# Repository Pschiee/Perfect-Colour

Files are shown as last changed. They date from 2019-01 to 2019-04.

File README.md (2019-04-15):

<p align="center">
	<a href="https://enquiriesperfectco.wixsite.com/perfectcolour">
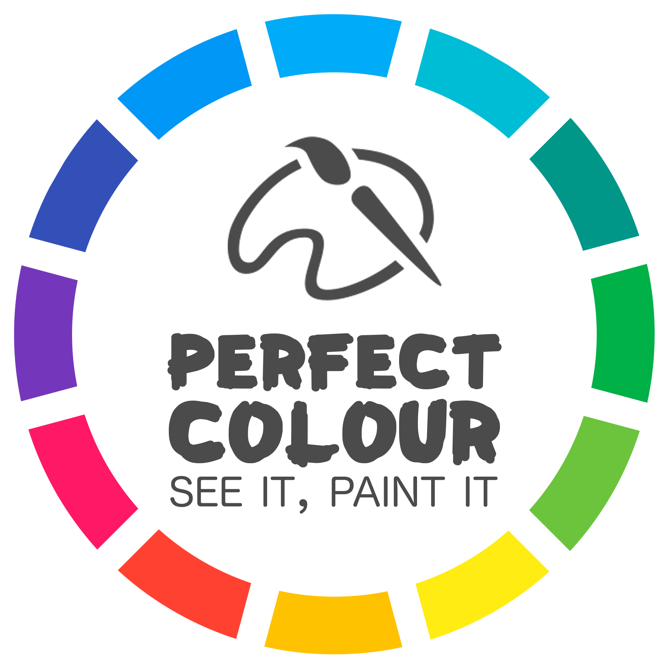
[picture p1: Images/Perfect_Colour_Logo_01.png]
Perfect Colour
	</a></p>

<!-- display the social media buttons in your README -->

[][1]
[][2]

<!-- links to social media icons -->
<!-- no need to change these -->

<!-- icons with padding -->

[1.1]: http://i.imgur.com/tXSoThF.png (twitter icon with padding)
[2.1]: http://i.imgur.com/P3YfQoD.png (facebook icon with padding)

<!-- links to your social media accounts -->
<!-- update these accordingly -->

[1]: https://twitter.com/PerfectColour1
[2]: https://www.facebook.com/Perfect-Colour-2317584661807012/

# Perfect Colour 

Welcome to the Github for Perfect Colour - The paint system to automatically dispense the colour of paint that you want.

<p align="center">
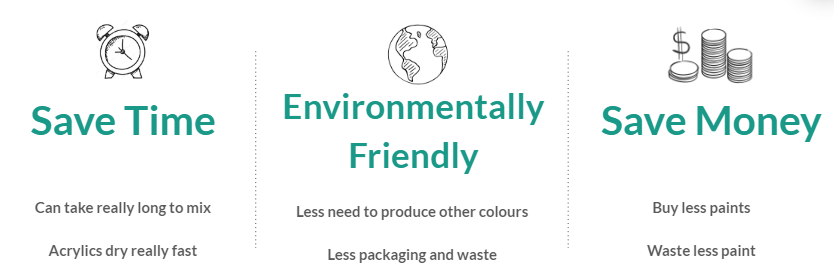
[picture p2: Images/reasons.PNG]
	</a></p>

Through the use of the GUI, you can select the colour using two different methods: by using the colour wheel or by selecting the colour you wish on an image which can then be made for you. 

# Table of Contents
1. [Installation](#installation)
2. [How to get started](#how-to-get-started)
3. [Using the application](#using-the-application)
4. [Demonstrartion](#demonstration)
5. [FAQs](#faqs)
6. [Further Information](#further-information)
7. [Credits](#credits)

## Installation

On the terminal of a Raspberry Pi type the following:

`git clone https://github.com/Pschiee/Perfect-Colour.git`

`cd Software`

`qmake`

`make`

`./AppPerfectColour`

QT and wiringPi are required.

## How to get started

Once you own a Perfect Colour Machine, follow 3 simple steps:
1. Obtain the 5 primary paints and load them to the machine
2. Open our app
3. Choose your colour and click "mix"

## Using the application

Very simple! Follow the following steps:
1. Open the application on your PC
2. Select a colour on the wheel or by uploading a picture and choosing it from it.
3. Specify the quantity of paint you want
4. Click mix and voila!

For further information please visit the <a href="https://github.com/Pschiee/Perfect-Colour/wiki/User-Manual">User Manual</a>.

## Demonstration

<a href="https://www.youtube.com/watch?v=QNqFCe46agE" target="_blank"> Water Test </a>

<a href="https://www.youtube.com/watch?v=BCwkkFHPxvM" target="_blank"> Paint Test </a>

## FAQs

**- Is there a phone appliacation available?**

There is no applications available for phones or tablets at the moment. However, we do consider this for a future development.

**- Can other types of paints be used?**

The machine is designed to produce colours from five colours of acrylic paints. The accuracy might vary with the quality and types of paint used. However, this can be addressed through calibration. Other paints like oil could obtain similar colours, however, due to the design of the machine, the results would not be the same.

**- Can I choose the exact colour I want?**

Indeed. You can either choose it within a palette or even take a picture and select the exact a colour from the desired pixel.

**- Can any colour be produced?**

Yes! CMYK plus white, when mixed correctly, can produce any colour. However, bear in mind this is dependant on the paints you are using, as if you use very matte primary colours, you will not be able to produce a bright gold, so choose your primary CMYK carefully.

**- Does the machine produce the colour I see or the real colour?**

The machine will produce the colour you see, so it will depend on the lighting conditions you took the picture in. Bare in mind that if what you want is the real colour instead, you would have to balance the whites of the picture before uploading it.

## Further Information

For all further information please visit our <a href="https://github.com/Pschiee/Perfect-Colour/wiki">Wiki</a>. 

For software documentation please click <a href="https://pschiee.github.io/Perfect-Colour/">here</a>. 

Or visit our <a href="https://enquiriesperfectco.wixsite.com/perfectcolour">website</a>.

Can also check out our <a href="https://www.instagram.com/perfect_colour_paint/">instagram</a>.

## Credits

<p align="right">

**- Callum Peter Mason:**

<p align="left">
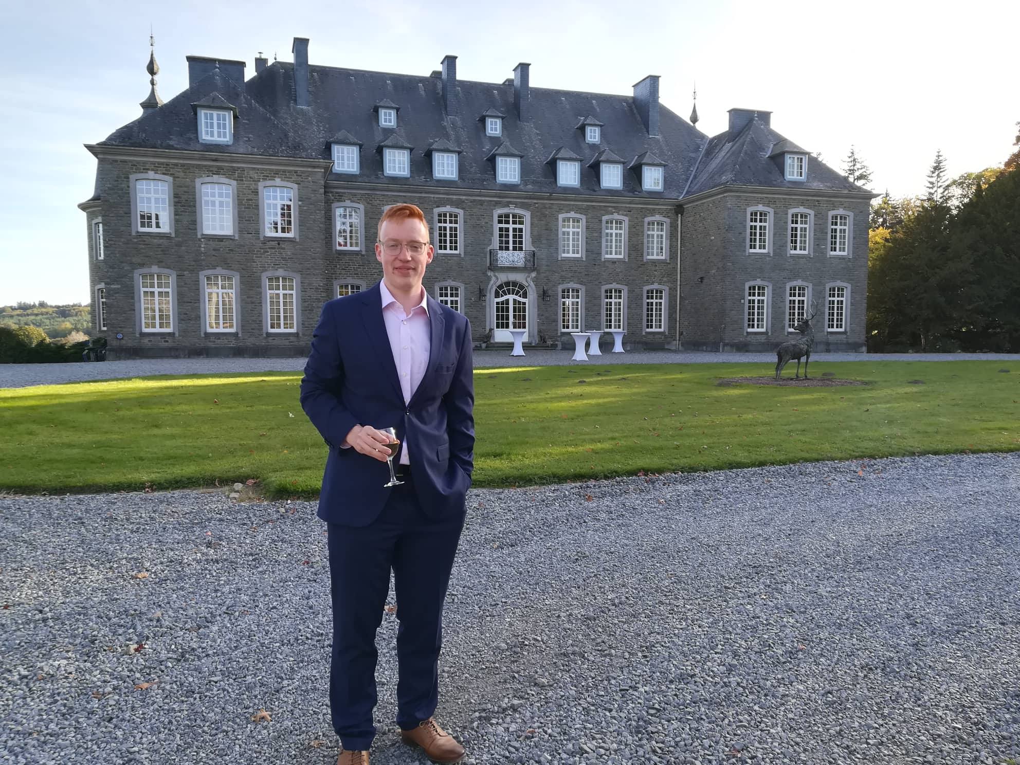
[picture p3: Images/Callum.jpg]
Callum
	</a></p>
<p align="left">
Software Engineer	 
	 
**- Silviya Ivanova:** 

<p align="left">
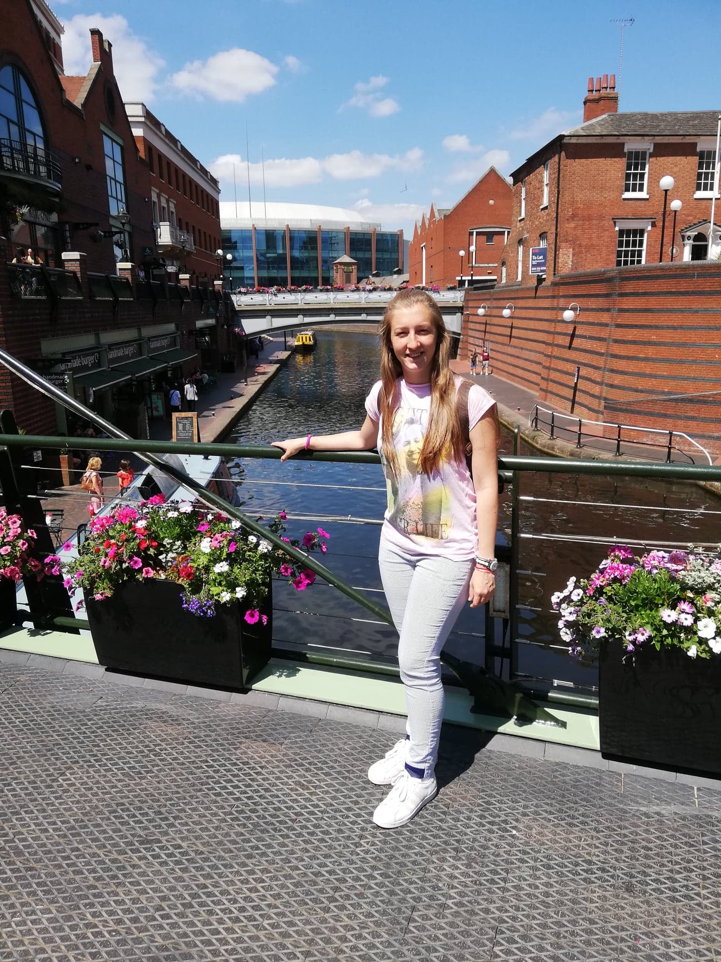
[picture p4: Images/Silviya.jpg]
Silviya
	</a></p>
<p align="leftr">
PCB Engineer

**- Leire Froufe Vigara:**

<p align="left">
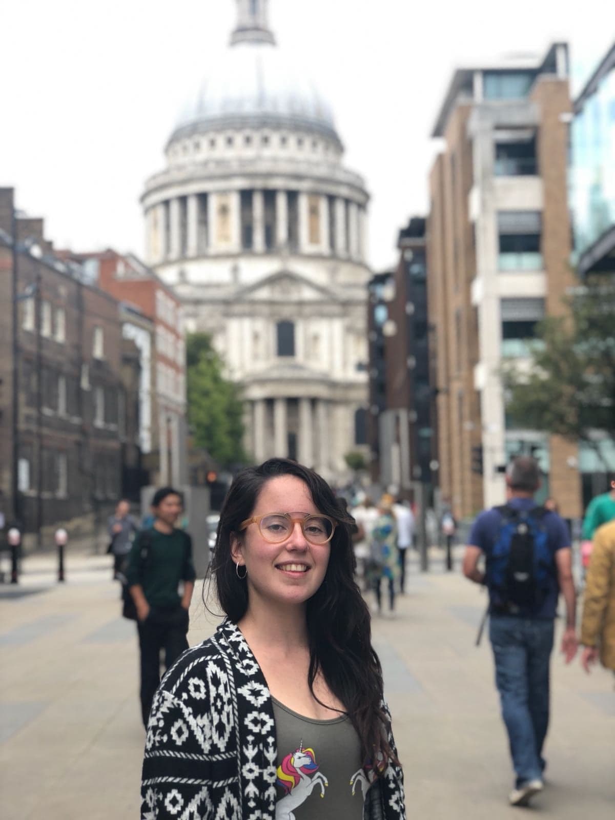
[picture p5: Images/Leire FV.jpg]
Leire
	</a></p>
<p align="left">
Mechanical Engineer and Marketing

 <p align="right">
 Perfect Colour</a></p>

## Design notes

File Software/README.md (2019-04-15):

**This folder contains the code to run the Perfect Colour application.**

To run:

`qmake`

`make`

`./AppPerfectColour`

The folder test contains the unit tests that were created for the weight sensor, stepper motor and colour calculations.

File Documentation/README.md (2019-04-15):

**This folder contains the documentation of the full electronic design.**

It is split into two main folders - PCB_Design and Schematics. These are further split into sub-folders which split the project into its two main stages - prototype and final. Initially, two prototype electronic designs were created for testing the motors (stepper and DC) and the load cell. Later on, it was decided that these should be merged in one design which was a Raspberry Pi shield PCB. This was the final design and its integration with the Raspberry Pi can be seen in the figure below:

<p align="left">
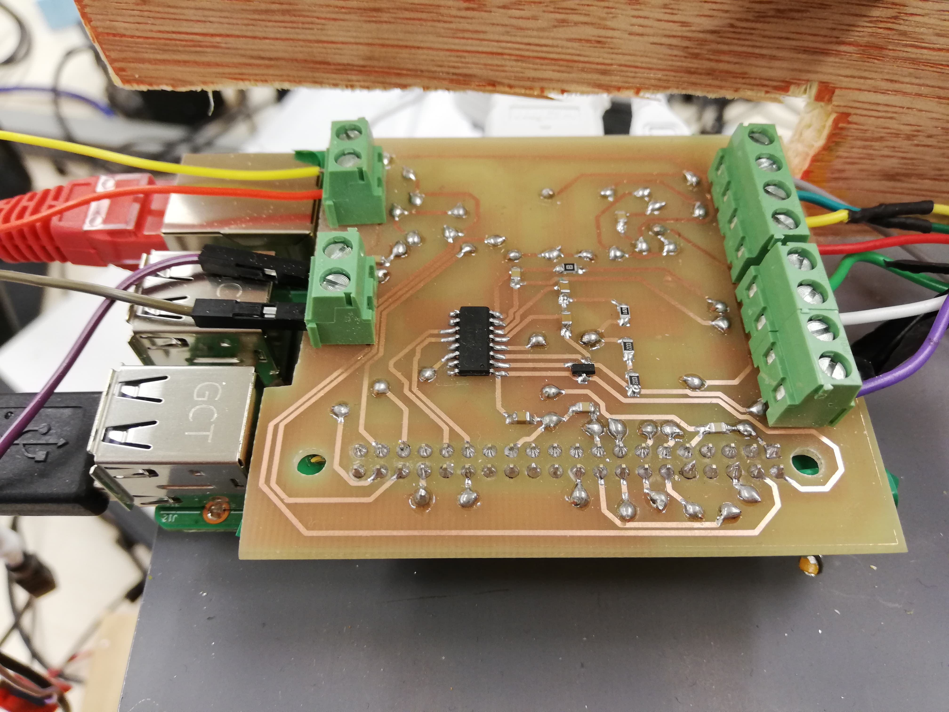
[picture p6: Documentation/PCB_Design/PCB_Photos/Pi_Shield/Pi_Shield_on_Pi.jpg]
Pi Shield on Pi
	</a></p>

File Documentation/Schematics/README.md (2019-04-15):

**This folder contains the schematics used for the electronic design throughout this project.**

The folders here contain the following:

- Pi_Shield_Schematic: features the files used for the final schematic of the PCB which fits on top of the Raspberry Pi.

- Stepper_Motor_Prototype: features the files used for the schematic of the prototype electronic design for the stepper and DC motor.

- Weight_Sensor_Prototype: features the files used for the schematic of the prototypeelectronic design  for the weight sensor.

- PDF_Schematics: features the pdf files which capture the three schematics.

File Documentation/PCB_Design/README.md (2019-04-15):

**This folder features all the files created for the electronic PCB design.**

Its content is split into three folders:

- PCB_Photos is a folder which contains post-manufacturing images taken of the PCB designs.

- PCB_Prototypes contains the files used for creating the PCB prototype designs.

- Pi_Shield_PCB has the files used for the final PCB design which is used on top of the Raspberry Pi and fits as a shield.

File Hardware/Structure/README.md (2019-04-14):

# Mechanical Design

Parts of the mechanical design have been designed and assembled using Solidworks. 
	 
## Contents
 **1. Design Description**
 
**2. Parts**

**3. Manufacturing**
 
 **4. Preview**
 
 **5. Further Information**
 
 ##  1. Design Description
 The Perfect Colour Machine consists of a caroussel that holds 5 syringes containing the CMYK(Cyan, Magenta, Yellow and Key) plus white colours.The caroussel is held up by a table-like structure and the paint is disposed onto a palette (or plate) which is on top of a weight sensor.
 
 ## 2. Parts
 The main parts of the structure are summarised below:
 - **Syringes** 
  <p align="left">
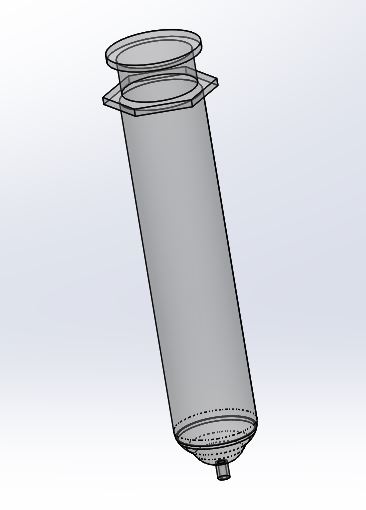
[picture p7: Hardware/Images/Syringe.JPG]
Syringe
 </a></p>

- **Carroussel** 
  <p align="left">
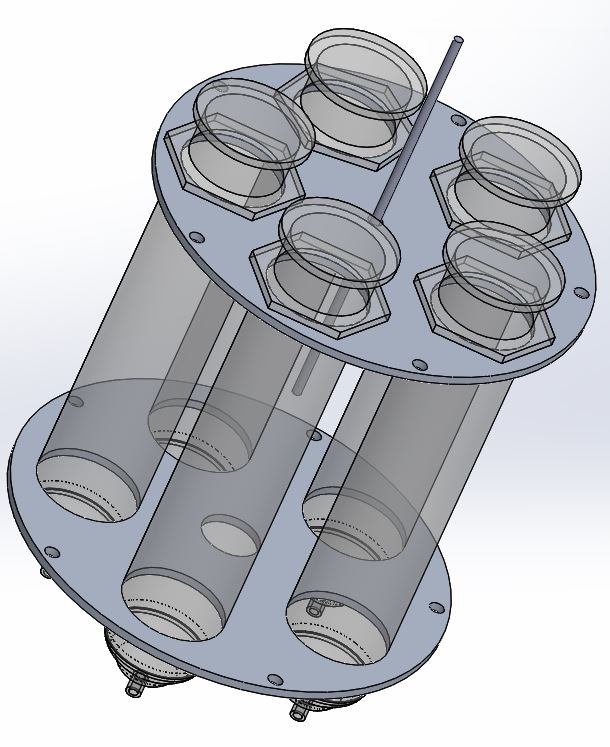
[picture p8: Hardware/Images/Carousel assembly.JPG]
Caroussel
 </a></p>
 
 - **Main structure**
 <p align="left">
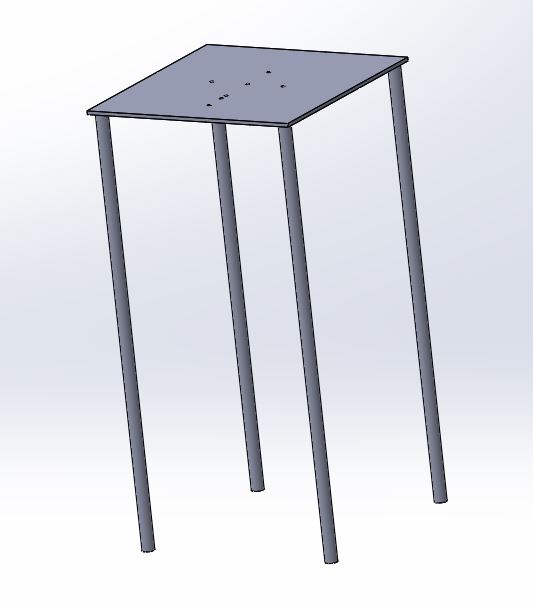
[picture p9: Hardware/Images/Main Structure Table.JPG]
Main Structure
 </a></p>

- **Attachment parts** 
  <p align="left">
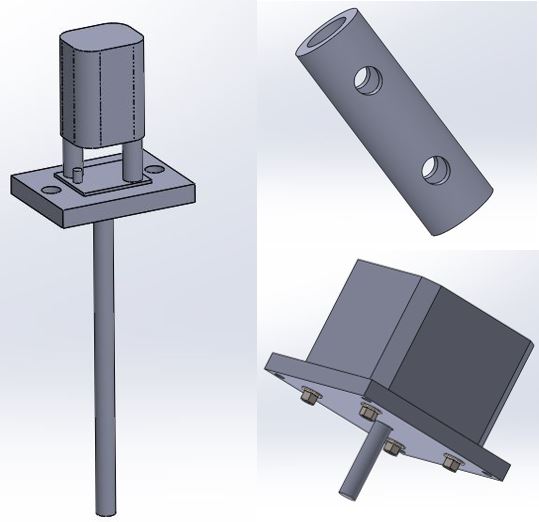
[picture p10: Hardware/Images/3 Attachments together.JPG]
3 attachments
 </a></p>
 
 ## 3. Manufacturing
 
 The parts were manufactured individually using different materials. However, aluminium was used for the most important parts to make it more durable. Other materials might not be able to withstand the torques produced by the spin of the caroussel. Therefore, the caroussel was manufactured in aluminium and aluminium rods were used for all connections.
 
 ## 4. Preview
 <p align="center">
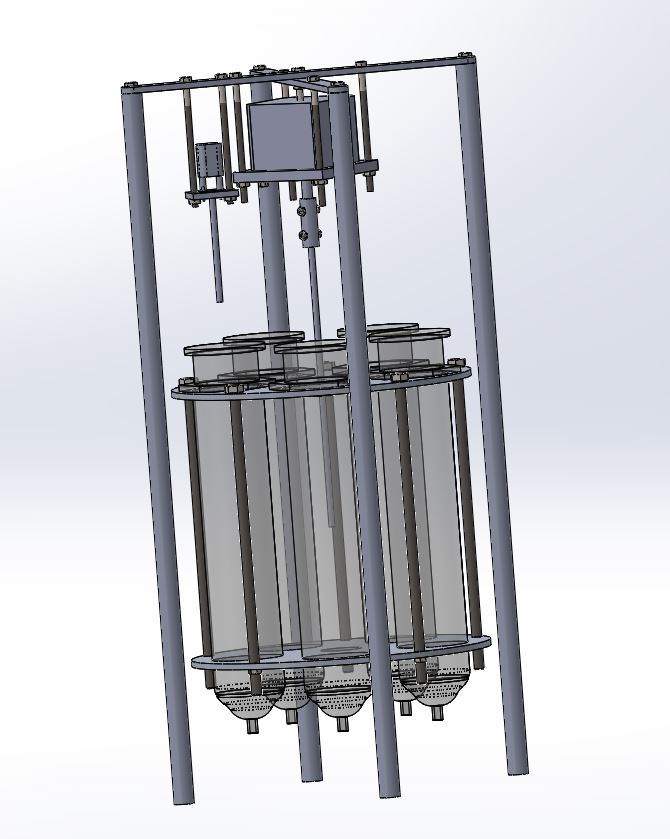
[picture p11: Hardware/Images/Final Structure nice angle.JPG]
Final Structure
 </a></p>

## 5. Further Information
For further information check out the <a href="https://github.com/Pschiee/Perfect-Colour/wiki/Hardware">Wiki Hardware</a>.

 <p align="right">
 Perfect Colour</a></p>

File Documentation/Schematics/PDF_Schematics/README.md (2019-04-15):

**This folder has the pdf files of the schematics created throughout this project.**

These include:

- Pi_PCB_Final: features the electronic design used for the final PCB which is fitted on top of the Raspberry Pi.

- motor_driver: features the schematic of the prototype used for the stepper and DC motors.

- weight_sensor: features the schematic of the prototype used for the weight sensor.

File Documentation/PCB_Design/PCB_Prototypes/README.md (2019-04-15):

**This folder features all the files created for the prototype electronic PCB design for the project.**

It is further split into two folders for the two prototype PCBs:

- Stepper_Motor is a folder which contains files of the stepper motor PCB prototype design.

- Weight_Sensor contains the prototype PCB design used for the weight sensor.

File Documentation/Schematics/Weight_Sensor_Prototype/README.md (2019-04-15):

**The files in this folder contain the prototype electronic design created for the weight sensor used for the project.**

It implements the following:

- Chip: HX711.

- Resistors: two 10kOhm, one 1kOhm and one 8.2kOhm.

- PNP transistor.

- Capacitors: three 1microFarad and one 100nanoFarad.

- Connections: two 4-pin MOLEX connectors.

**File names and description as follows:**

- weight_sensor_schematic.opj: features the full project file.

- WEIGHT_SENSOR_SCHEMATIC.DSN and WEIGHT_SENSOR_SCHEMATIC_0.DBK: are "make" files automatically generated by OrCAD.

- 100NF_CAPACITOR.OLB and 100NF_CAPACITOR_0.OBK: feature the 100nanoFarad ceramic surface mount capacitor.

- 10K_RESISTOR.OLB and 10K_RESISTOR_0.OBK: feature the 10kOhm surface mount resistor.

- 1K_RESISTOR.OLB and 1K_RESISTOR_0.OBK: feature the 1kOhm surface mount resistor.

- 1UF_CAPACITOR.OLB and 1UF_CAPACITOR_0.OBK: feature the 1microFarad ceramic surface mount capacitor.

- 8K2_RESISTOR.OLB and 8K2_RESISTOR_0.OBK: feature the 8.2kOhm surface mount resistor.

- HX711.OLB and HX711_0.OBK: feature the HX711 weight sensor chip.

- MOLEX_4.OLB, MOLEX_4_0.OBK, MOLEX_4_1.OLB and MOLEX_4_1_0.OBK: feature the 4-pin MOLEX connectors.

- PNP_TRANSISTOR.OLB and PNP_TRANSISTOR_0.OBK feature the PNP transistor.

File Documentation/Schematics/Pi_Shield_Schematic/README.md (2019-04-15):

**This folder contains the files used for the prototype electronic design for the stepper motor.**

All components featured are surface mount apart from the terminal connectors through which the stepper and DC motors and the load cell are connected to the board. The following components are used for this electronic design:

- Chips: HX711 and two L298.

- Resistors: two 10kOhm, one 1kOhm and one 8.2kOhm.

- Transisotr: a surface mount PNP.

- Capacitors: three ceramic 1microFarad, five ceramic 100nanoFarad and four electrolytic 1microFarad.

- Diodes: twelve 1N5814 surface mount diodes.

- Connections: one 4-pin and two 2-pin terminal connectors.

**File names with description:**

- raspberry_pi_shield.opj: features the full project file.

- RASPBERRY_PI_SHIELD.DSN and RASPBERRY_PI_SHIELD_0.DBK: are "make" files automatically generated by OrCAD.

- allegro folder: features files used to link schematic to PCB design.

- LIBRARY1.OLB and LIBRARY1_0.OBK: feature Pi header.

- LIBRARY2.OLB and LIBRARY2_0.OBK: feature the surface mount L298p motor driver chip.

- LIBRARY3.OLB and LIBRARY3_0.OBK: feature the 1kOhm surface mount resistor.

- LIBRARY4.OLB and LIBRARY4_0.OBK: feature the 1microFarad electrolytic capacitor.

- LIBRARY5.OLB and LIBRARY5_0.OBK: feature the 1N5814 surface mount diode.

- LIBRARY6.OLB and LIBRARY6_0.OBK: feature the 2-pin terminal connector.

- The rest of the components are used as generated for the prototype schematics.

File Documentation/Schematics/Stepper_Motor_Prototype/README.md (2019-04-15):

**This folder contains the files used for the prototype electronic design for the stepper motor.**

It features the following:

- Chip: L298 motor driver.

- Capacitors: two ceramic 100nanoFarad and two electrolytic 1microFarad.

- Connections: one 4-pin and five 2-pin MOLEX connectors.

- Diodes: eight through hole diodes (for the two H-bridge rectifiers).

**File names with description:**

- stepper_motor_schematic_prototype.opj: features the full project file.

- STEPPER_MOTOR_SCHEMATIC_PROTOTYPE.DSN, STEPPER_MOTOR_SCHEMATIC_PROTOTYPE.DSNlck and STEPPER_MOTOR_SCHEMATIC_PROTOTYPE_0.DBK: are "make" files automatically generated by OrCAD.

- allegro folder: features files used to link schematic to PCB design.

- l298n folder: features schematic for L298N chip (through hole).

- CAP_E.OLB, CAP_E.OLBlck and CAP_E_0.OBK: feature schematic for 1microFarad electrolytic capacitor.

- LIBRARY4.OLB, LIBRARY4.OLBlck and LIBRARY4_0.OBK: feature schematic for 4-pin MOLEX connector.

- LIBRARY1.OLB, LIBRARY1.OLBlck, LIBRARY1_0.OBK, MOL2.OLB, MOL2.OLBlck and MOL2_0.OBK: feature schematic for 2-pin MOLEX connector.

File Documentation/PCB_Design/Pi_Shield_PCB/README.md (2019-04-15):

**This folder contains the files created for the stepper/DC motor prototype PCB.**

Files with description as follwos:

- Top_Pi_Board and Bottom_Pi_board feature the photomasks used for manufacturing of the PCB top and bottom respectively.

- Shield_for_Pi is the cadence file that has the PCB design.

- Raspberry_Pi_Shield is a screenshot of the final design.

<p align="left">
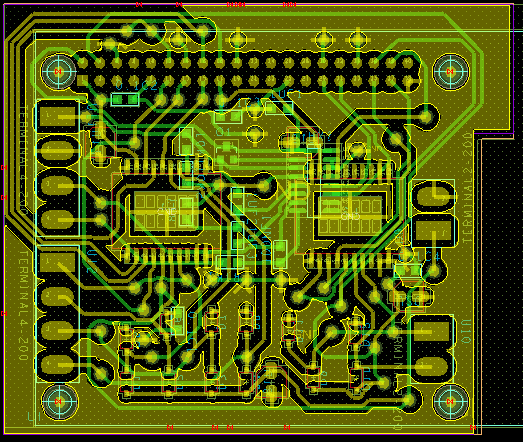
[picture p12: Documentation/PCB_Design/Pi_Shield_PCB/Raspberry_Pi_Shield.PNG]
Raspberry Pi Shield
	</a></p>

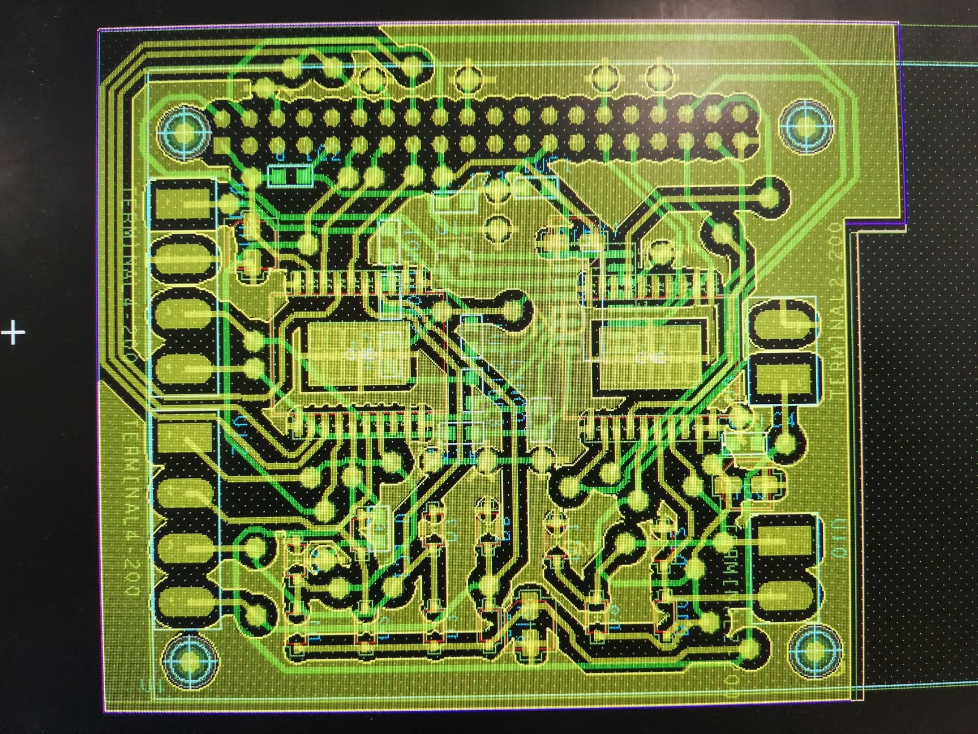
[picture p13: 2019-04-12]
Images/PCB Final Design 1.jpg

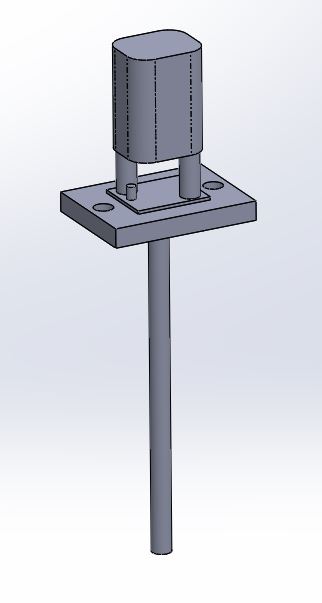
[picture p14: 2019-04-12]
Hardware/Images/Linear Actuator plus attachment.JPG

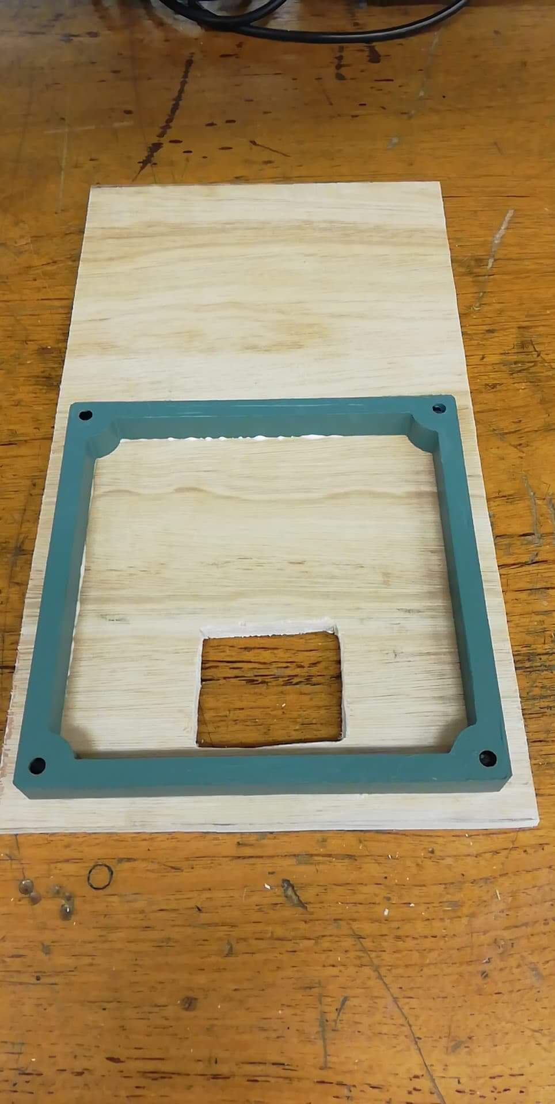
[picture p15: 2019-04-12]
Hardware/Images/Wooden Frame 2.jpeg

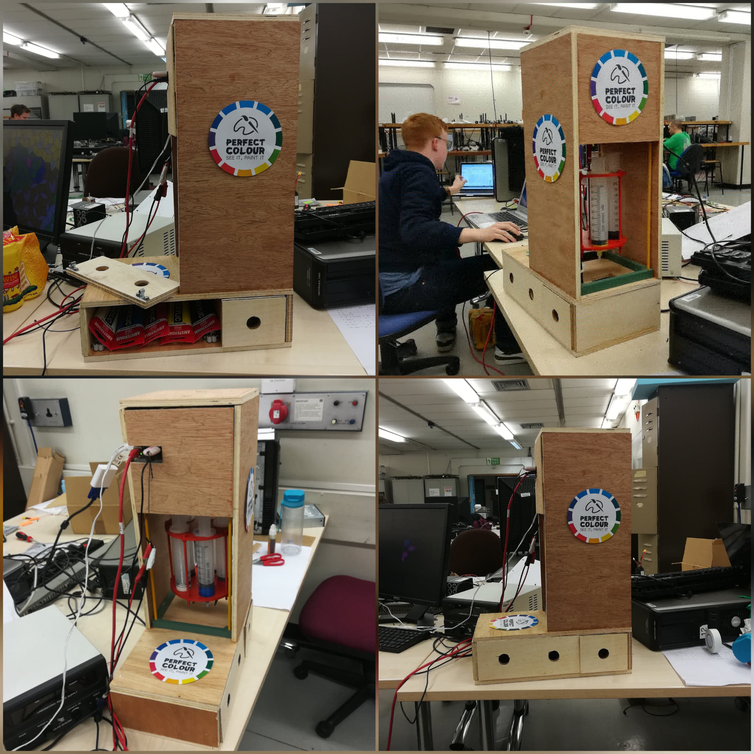
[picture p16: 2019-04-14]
Hardware/Images/Final Product Collage.jpg

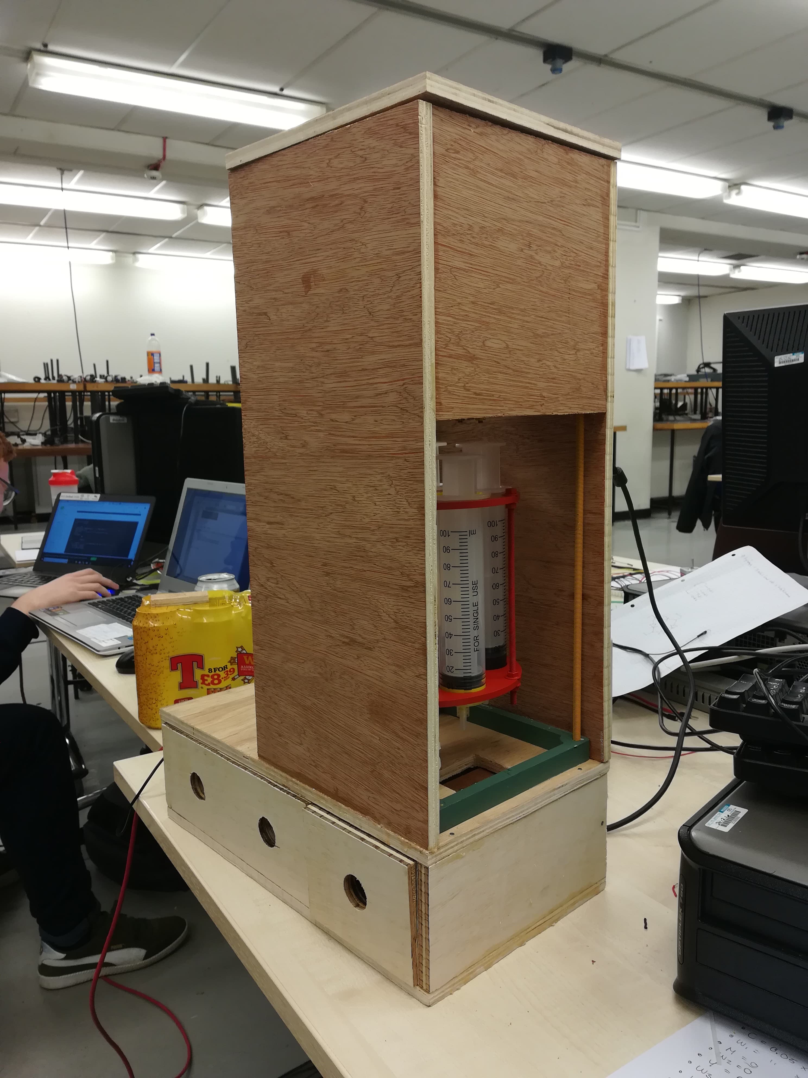
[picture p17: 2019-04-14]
Hardware/Images/Final Structure 1.jpg

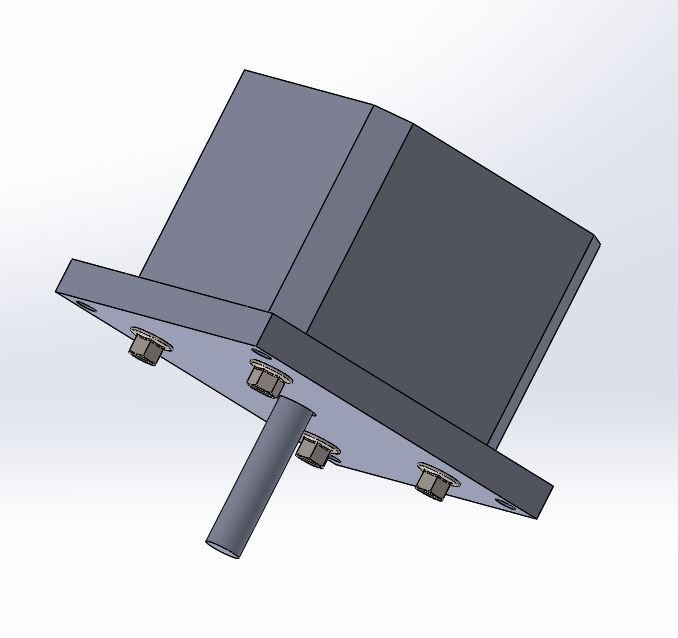
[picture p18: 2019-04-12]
Hardware/Images/Motor plus attachment.JPG

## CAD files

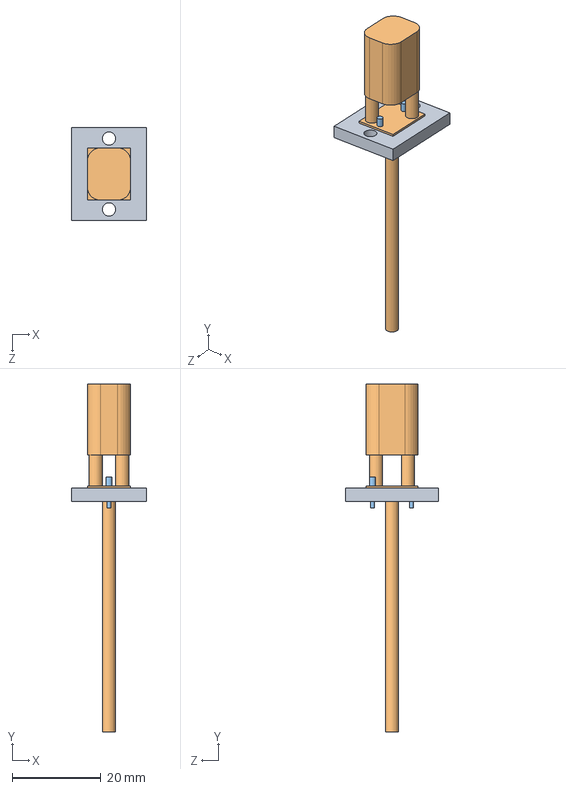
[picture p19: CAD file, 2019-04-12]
Hardware/Structure/Linear actuator plus assembly.SLDASM
17.0 x 78.5 x 21.0 mm
Linear Actuator attachement
Linear actuator
1mm tube x 2

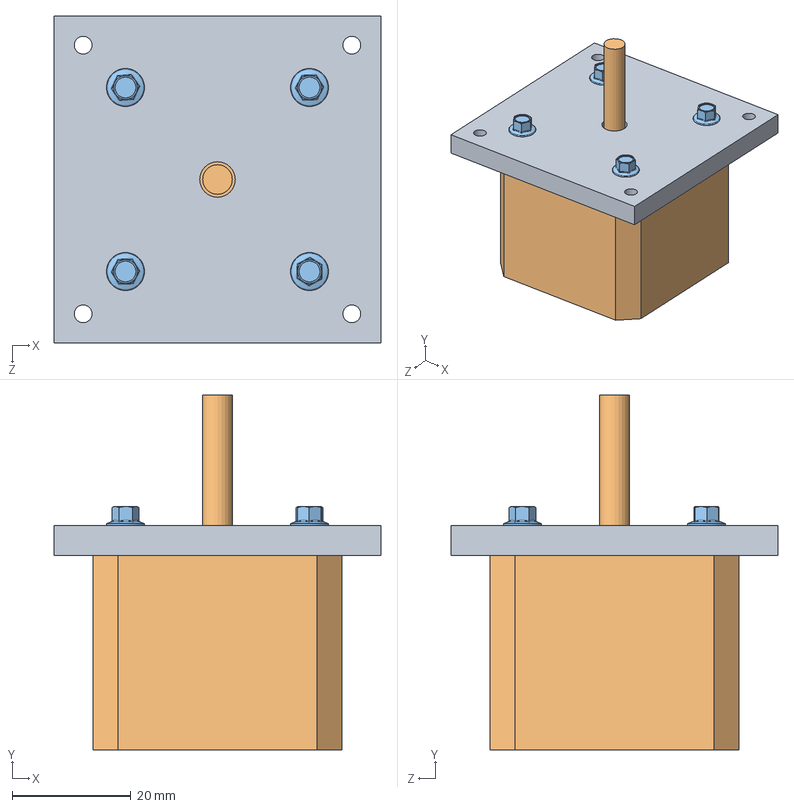
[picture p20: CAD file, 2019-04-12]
Hardware/Structure/Motor plus Mototr assembly.SLDASM
55.0 x 59.8 x 55.0 mm
Motor and structure Mount
Stepper Motor
hex flange machine screw_am x 4

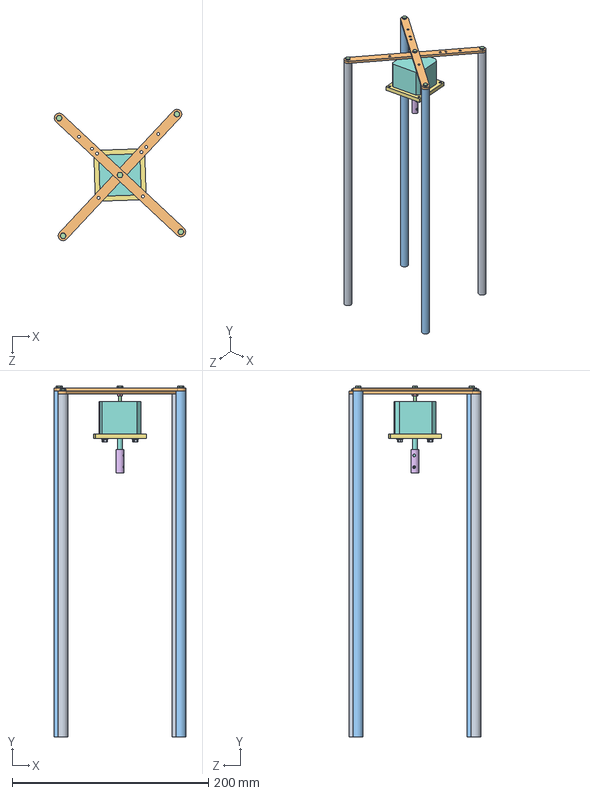
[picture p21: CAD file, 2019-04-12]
Hardware/Structure/Structure Assembly.SLDASM
134.1 x 358.0 x 134.1 mm
Stucture Leg x 2
Top of structure x 2
Stucture Leg Taller x 2
hexagon head bolt (grades a and b)_as x 5
hexagon nut style 1 (grades a and b) as
Shaft Adjuster
Motor and structure Mount
Stepper Motor
hex flange machine screw_am x 4

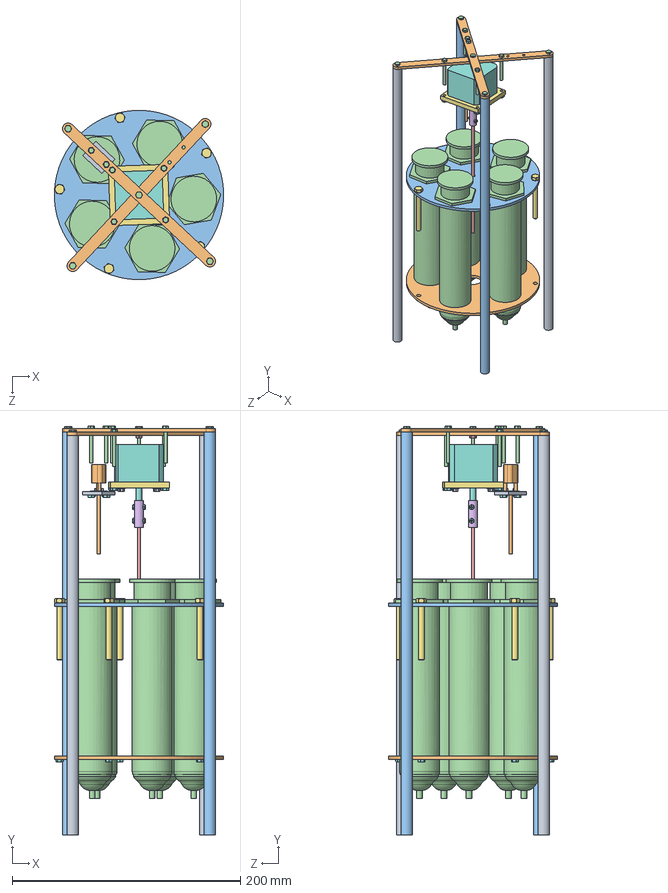
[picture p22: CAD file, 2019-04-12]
Hardware/Structure/Final Assembly.SLDASM
148.3 x 358.3 x 148.3 mm
Stucture Leg x 2
Top of structure x 2
Stucture Leg Taller x 2
hexagon head bolt (grades a and b)_as x 5
hexagon nut style 1 (grades a and b) as
Shaft Adjuster
Motor and structure Mount
Stepper Motor
hex flange machine screw_am x 4
Syringe Plate 2
Syringe Plate 2 - Copy
Syringe x 5
Carouseel axis Rod
hex flange nut_am
hex bolt gradec_as x 5
hex nut style 1_am x 15
Linear Actuator attachement
Linear actuator
1mm tube x 2
hex screw_am x 6

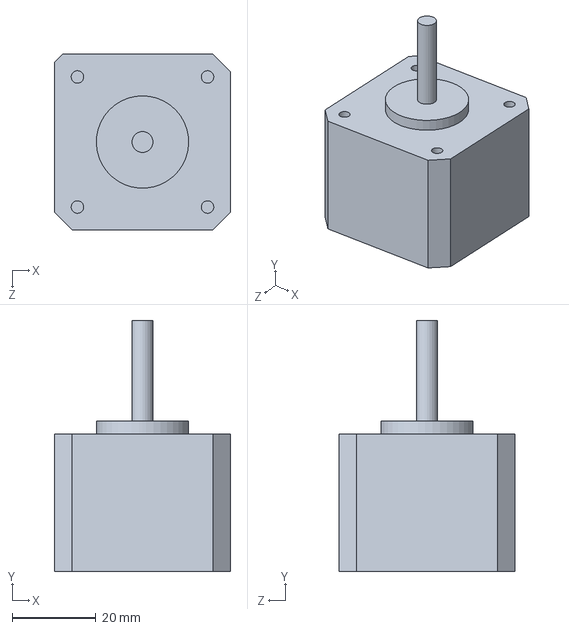
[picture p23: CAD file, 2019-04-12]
Hardware/Structure/Stepper Motor.SLDPRT
42.0 x 59.8 x 42.0 mm

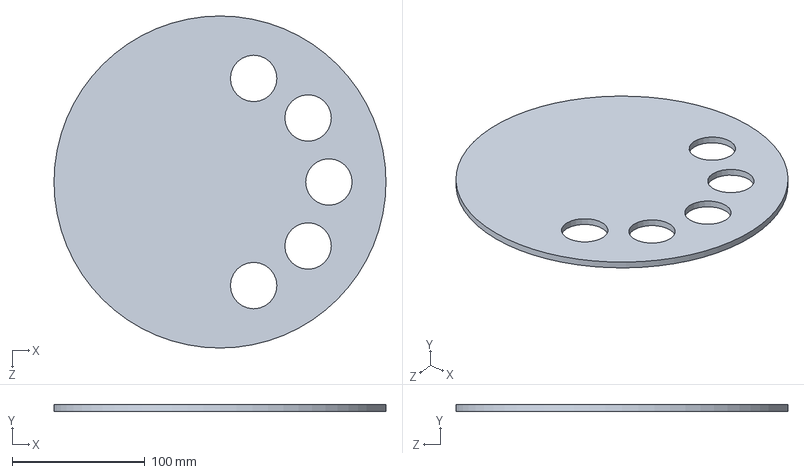
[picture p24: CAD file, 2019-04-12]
Hardware/Structure/Syringe Plate.SLDPRT
250.0 x 5.00 x 250.0 mm

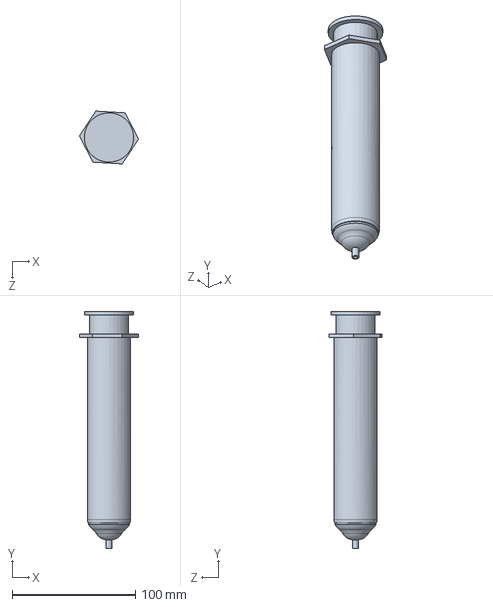
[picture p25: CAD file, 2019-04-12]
Hardware/Structure/Syringe.SLDPRT
47.9 x 192.4 x 42.9 mm

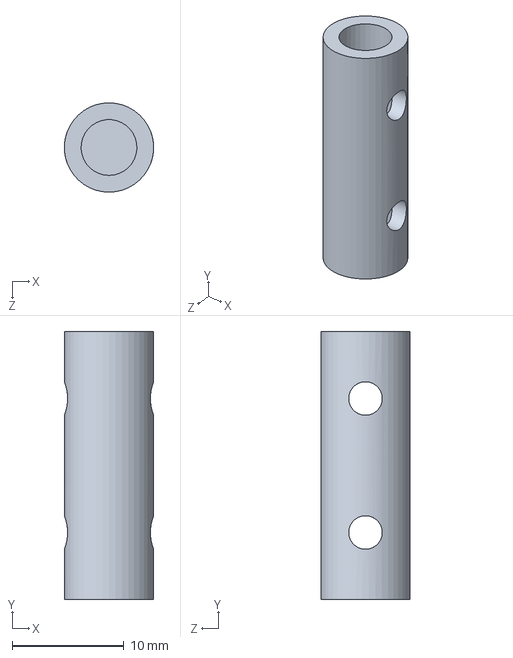
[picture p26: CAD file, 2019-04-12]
Hardware/Structure/Shaft Adjuster.SLDPRT
8.00 x 24.0 x 8.00 mm

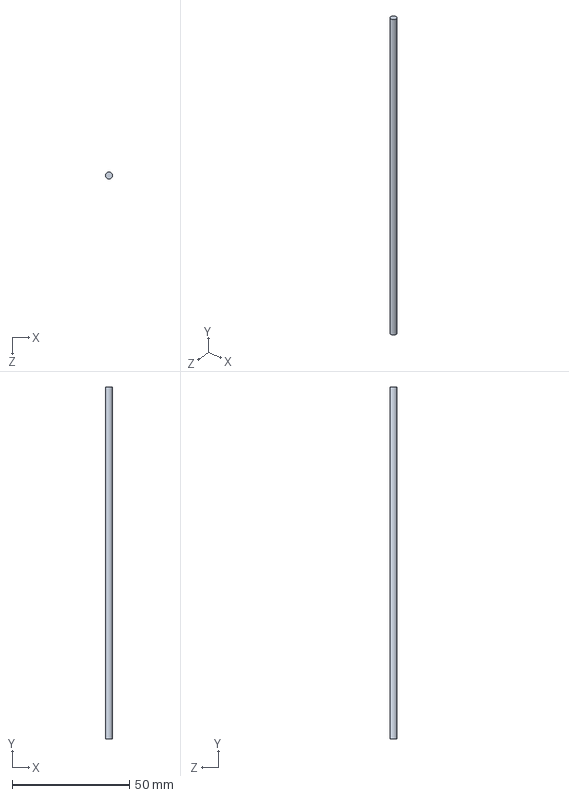
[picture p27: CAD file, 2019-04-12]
Hardware/Structure/Carouseel axis Rod.SLDPRT
3.00 x 150.0 x 3.00 mm

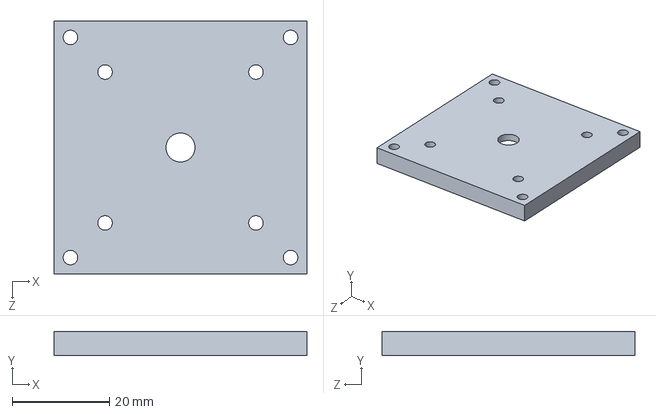
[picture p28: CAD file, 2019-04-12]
Hardware/Structure/Motor and structure Mount.SLDPRT
52.0 x 5.00 x 52.0 mm

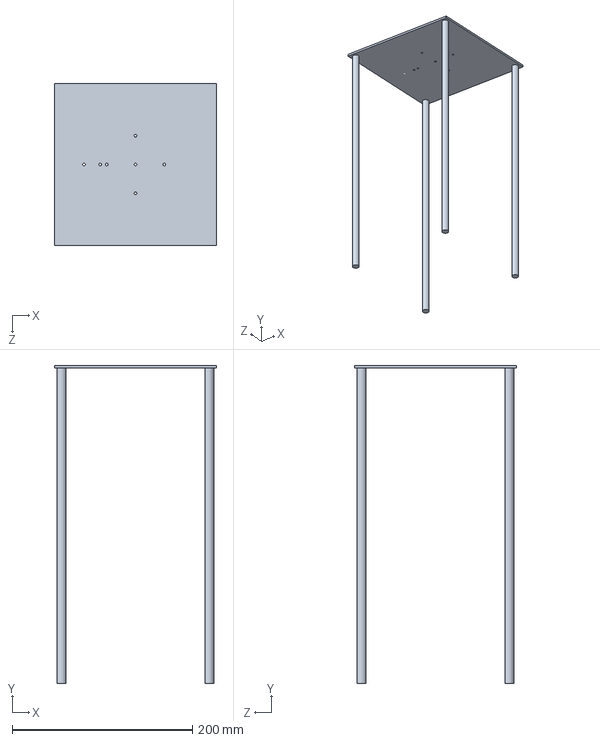
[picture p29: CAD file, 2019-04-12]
Hardware/Structure/Top of structure TABLE -.SLDPRT
180.0 x 353.0 x 180.0 mm

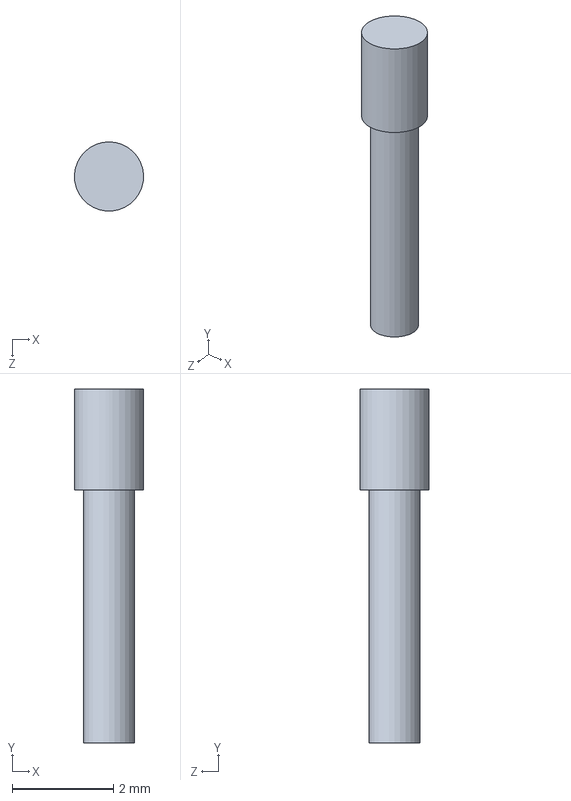
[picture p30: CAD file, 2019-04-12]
Hardware/Structure/1mm tube.SLDPRT
1.37 x 7.00 x 1.37 mm

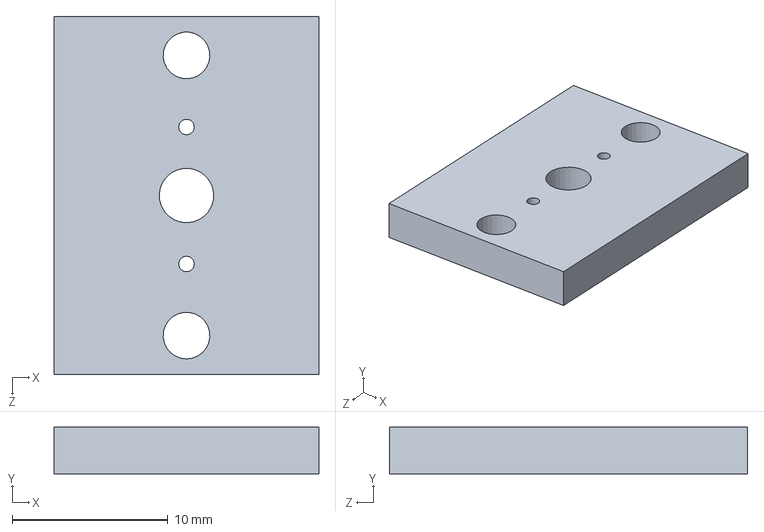
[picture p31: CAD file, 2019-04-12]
Hardware/Structure/Linear Actuator attachement.SLDPRT
17.0 x 3.00 x 23.0 mm

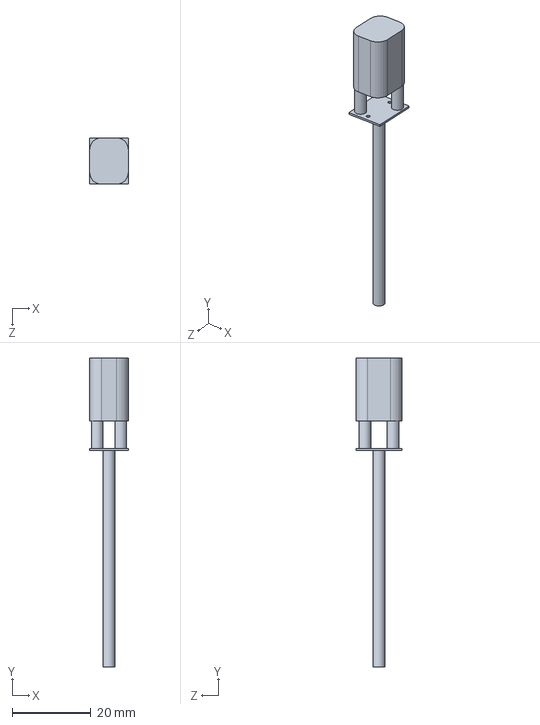
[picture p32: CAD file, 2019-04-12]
Hardware/Structure/Linear actuator.SLDPRT
9.80 x 78.5 x 11.8 mm

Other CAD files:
Hardware/Structure/Stucture Leg.SLDPRT
Hardware/Structure/Syringe Plate 2.SLDPRT
Hardware/Structure/Stucture Leg Taller.SLDPRT
Hardware/Structure/Top of structure.SLDPRT
Hardware/Structure/Syringe Plate 2 - Copy.SLDPRT
Hardware/Structure/hex bolt caroussel.sldprt
Hardware/Structure/hex screw fot shaft adapter.sldprt
Hardware/Structure/hex screw_am linear actuator.sldprt
Hardware/Structure/hex screw_motor attachment.sldprt

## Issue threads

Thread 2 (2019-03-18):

Weight sensor PCB

SilviyaGIvanova, 2019-03-18:
Weight sensor schematic and PCB missing a calibrating resistor

SilviyaGIvanova, 2019-03-27:
This was resolved by scratching off the track (this is a test PCB...) and adding the resistor to the board

Closed 2019-03-27.

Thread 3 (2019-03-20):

Problem with Motor driver

Pschiee, 2019-03-20:
PCB designed for motor driver may be incorrect. Needs checked

SilviyaGIvanova, 2019-03-27:
Problem was manufacturing issue and was resolved

Closed 2019-03-27.

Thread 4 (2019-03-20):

Lack of availability of materials

LeireFroufe, 2019-03-20:
In order to build a solid structure, aluminium is required, but it does not fit at all within the budget. Alternatives should be considered.

Closed 2019-03-20.

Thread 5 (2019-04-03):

Resolution of GUI on raspberry pi bad

Pschiee, 2019-04-03:
GUI on pi expands off the screen. Probably caused by image minimum size. Needs fixed

Pschiee, 2019-04-11:
Fixed with use of laptop as the display

Closed 2019-04-11.

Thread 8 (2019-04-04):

Initial PCB design - fine but not optimal

SilviyaGIvanova, 2019-04-04:
Separate PCBs were designed for the testing stage of the project, however, the team needed a PCB that would fit as a hat on the Raspberry Pi and would have similar dimensions. This would make the design more compact and appealing to the eye. Could everything fit on the bottom so it is hidden?

Pschiee, 2019-04-04:
It would be optimal if everything could be put on the one side however with the number of different components required on the board, this isn't going to be possible

SilviyaGIvanova, 2019-04-10:
This has been done (double-sided PCB was manufactured) and testing has begun.

Closed 2019-04-10.

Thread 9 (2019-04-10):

Stepper motor does not turn

SilviyaGIvanova, 2019-04-10:
Stepper motor was tested on the final PCB. Turned for a while then started turning forwards and backwards for no reason (?). Issue might be with the new PCB.

SilviyaGIvanova, 2019-04-10:
PCB has been checked. Nothing is causing a short-circuit.
Test motor on old PCB to make sure it is still working.

Pschiee, 2019-04-11:
Problem was on enable pin A. There was a thin track connecting this to ground and therefore half of the pins were disabled.

Closed 2019-04-11.

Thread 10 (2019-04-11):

Using colour wheel the colour is not dispensed. Only working with browse

Pschiee, 2019-04-11:
Should be a simple resolve with how the colour is being passed between functions.

Pschiee, 2019-04-14:
Changed so now the colour is stored using browse and colour wheel

Closed 2019-04-14.

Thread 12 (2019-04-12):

Case required to hold structure

SilviyaGIvanova, 2019-04-12:
To ensure that the carousel is protected we need to build a case that will support it and hide some electrical features from the user (safety/protection).

SilviyaGIvanova, 2019-04-14:
Done using wood plates to support the structure fully on the top, bottom, left and right. There is a gap opening from the front and back so that the user can see the paint being dispensed and easily pick the syringes out in case cleaning/refilling is needed.

Closed 2019-04-14.

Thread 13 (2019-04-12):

DC motor to become a linear actuator ("pusher")

SilviyaGIvanova, 2019-04-12:
How should the DC motor be mounted so that it pushes against the syringe to dispense paint? Initial design does not seem to account for this because the motor itself would spin instead of going up and down.

SilviyaGIvanova, 2019-04-14:
This is done through a threaded plate which is held onto the top plate of the structure via screw rods. As the motor spins the threaded rod it acts as a linear actuator and moves up and down (pushing against the syringe to dispense paint). The motor itself is constrained from spinning as it is placed between two aluminium plates which only allow it to slide.

LeireFroufe, 2019-04-14:
It works efficiently

SilviyaGIvanova, 2019-04-14:
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

Closed 2019-04-14.

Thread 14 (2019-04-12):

GUI does not account for cleaning/refilling requests

SilviyaGIvanova, 2019-04-12:
Include a dialog window which can be used by the user to request a paint refilling/cleaning of syringe.

SilviyaGIvanova, 2019-04-14:
Now done. GUI has a button on the main window which says "Clean/Refill" and clicking on it sends you to the cleaning/refilling dialog from where the user can select the colour that they need to refill. Once finished, they can return to the main window

Closed 2019-04-14.

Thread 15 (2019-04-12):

Storage space for paint/brushes

SilviyaGIvanova, 2019-04-12:
Can space be allocated for storing extra paint and accessories by the painter?

SilviyaGIvanova, 2019-04-14:
Storage space has been allocated at the back of the structure behind the weight sensor in a separate opening so that the objects inside do no interfere with the weight sensor. It provides space for all accessories needed by an artist.

Closed 2019-04-14.

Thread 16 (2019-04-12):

Mounting of weight sensor

SilviyaGIvanova, 2019-04-12:
What would be the best way to mount the weight sensor under the structure?

SilviyaGIvanova, 2019-04-14:
The weigh sensor has been fitted onto a platform under the carousel. It is accessible through a door opening on the side in case any reconfiguration is needed.

Closed 2019-04-14.

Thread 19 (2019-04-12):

Weight Sensor not working

LeireFroufe, 2019-04-12:
The weight sensor is now giving random values, but it was working the previous day.

SilviyaGIvanova, 2019-04-15:
Fixed through filtering and averaging.

Closed 2019-04-15.

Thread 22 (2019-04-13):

GUI crashes during weight sensing

Pschiee, 2019-04-13:
GUI crashes during weight sensing. Add threading.

SilviyaGIvanova, 2019-04-15:
Now added

Closed 2019-04-15.

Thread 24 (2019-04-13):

DC motor doesn't spin

Pschiee, 2019-04-13:
This happened before. Was an issue with code.

Closed 2019-04-14.

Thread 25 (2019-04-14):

Weight Sensor Overload

LeireFroufe, 2019-04-14:
Weight sensor stops working when too much paint is dispensed. Then it freezes.

LeireFroufe, 2019-04-14:
It now works.

Closed 2019-04-14.

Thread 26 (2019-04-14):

Rotations Inaccurate

LeireFroufe, 2019-04-14:
The syringes are not ending up underneath the DC motor on each rotation.

Pschiee, 2019-04-14:
A mechanical issue. Software is fine.

LeireFroufe, 2019-04-14:
Carousel had come loose, so it was rotating without the motor. Therefore going to wrong positions. It has been tightened.

LeireFroufe, 2019-04-14:
It now works. Small rotation due to surface area of the pusher being too small and sliding through the top of the syringe. We increased the surface area.

It works.

Closed 2019-04-14.

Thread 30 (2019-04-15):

Weight sensor wires

SilviyaGIvanova, 2019-04-15:
how do we send them up to the top of the structure where the Pi is?

SilviyaGIvanova, 2019-04-15:
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

The wires going from the load cell to the Raspberry Pi have been put through a heat shrink sleeve and 2 holes are drilled - one on the bottom under the carousel and the other one on the top aluminium plate.

Closed 2019-04-15.

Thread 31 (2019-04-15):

Raspberry Pi attachment to structure

SilviyaGIvanova, 2019-04-15:
We want it on top but what is the best way to do it?

SilviyaGIvanova, 2019-04-15:
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

SilviyaGIvanova, 2019-04-15:
It has been mounted using spacers. Holes have been drilled in the top metal plate so that the spacers can be fixed on it using bolts.

Closed 2019-04-15.

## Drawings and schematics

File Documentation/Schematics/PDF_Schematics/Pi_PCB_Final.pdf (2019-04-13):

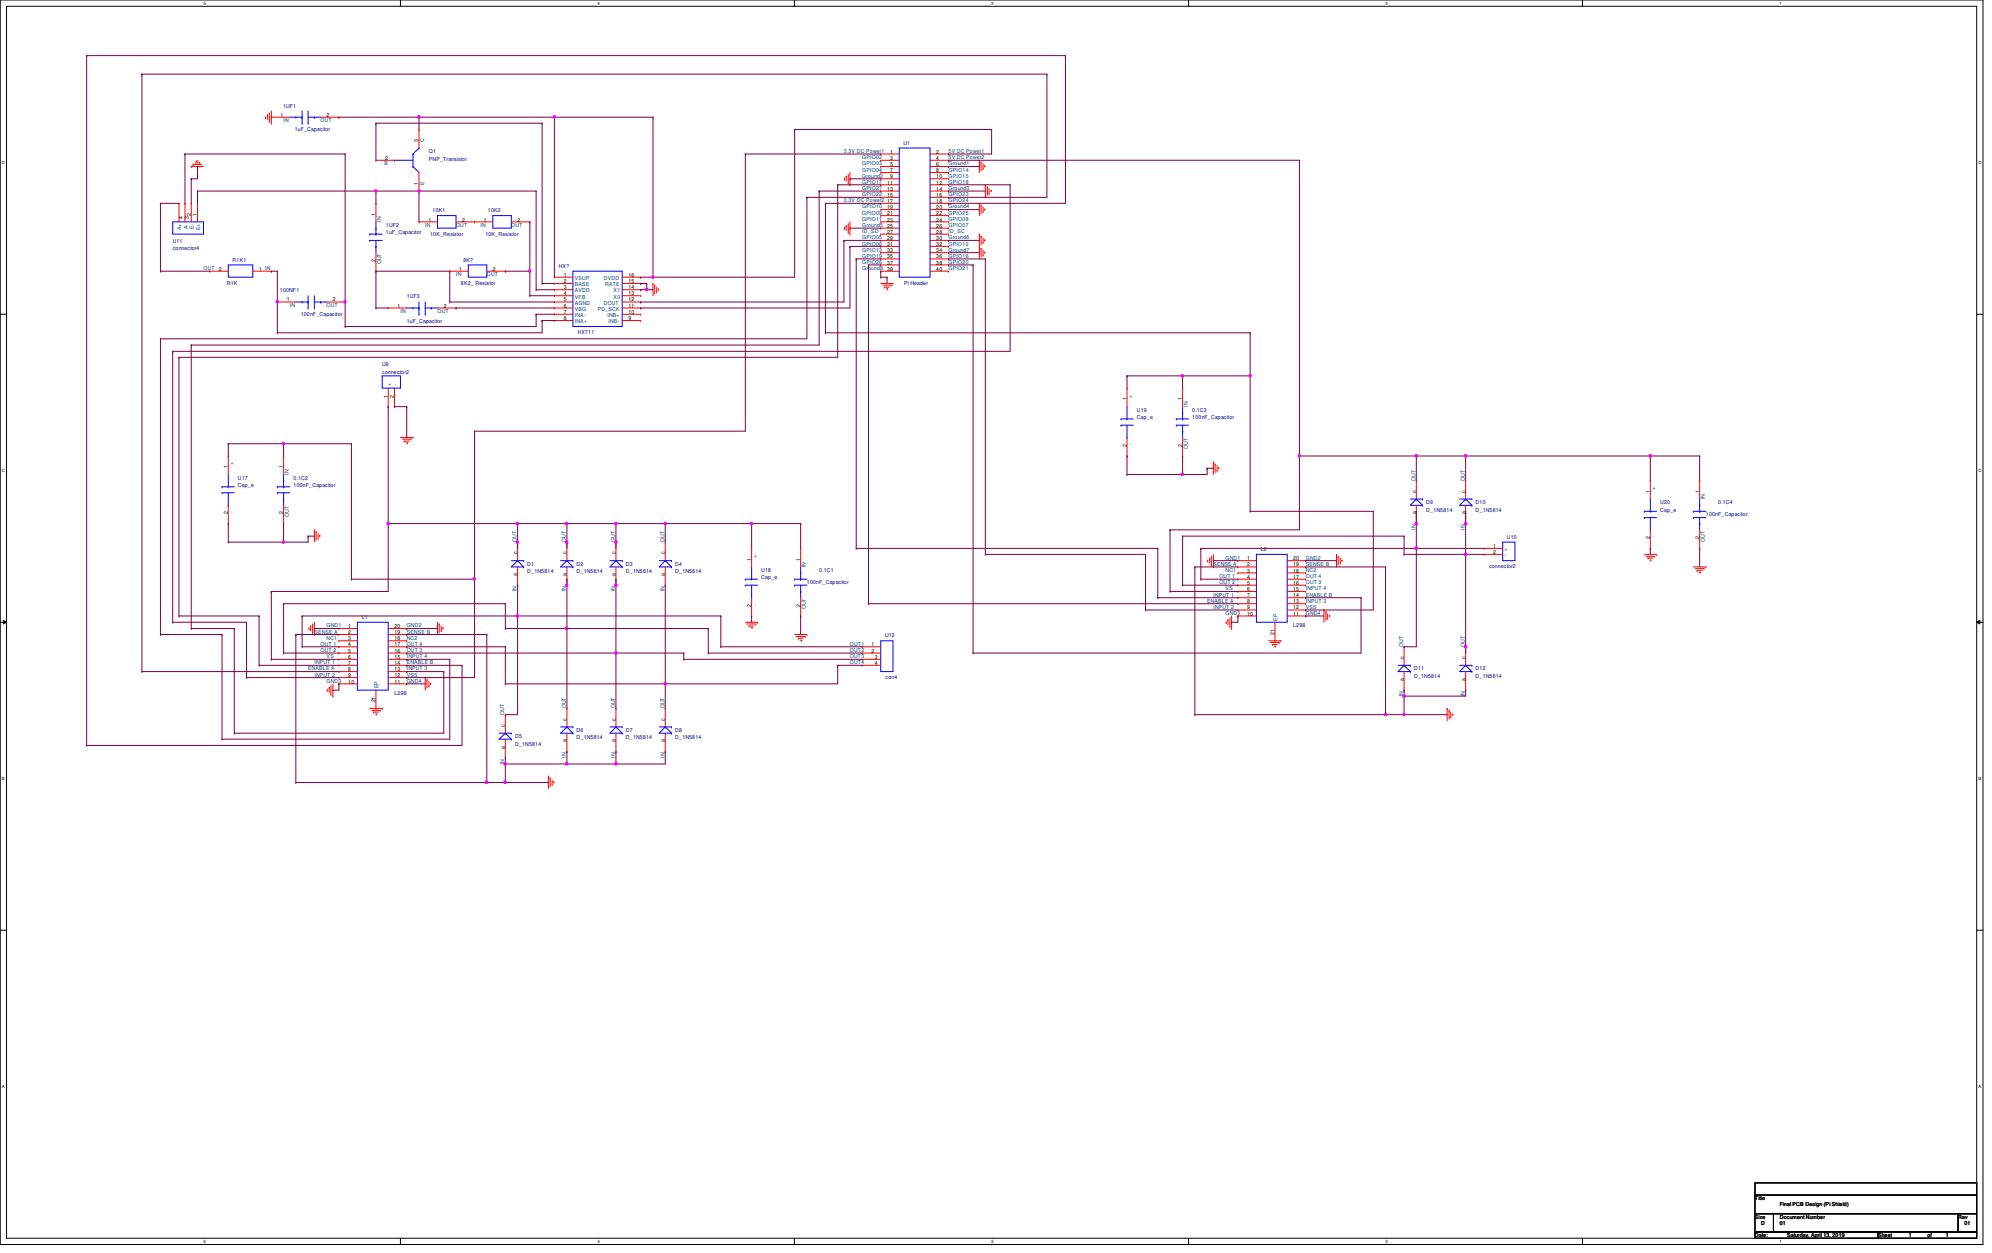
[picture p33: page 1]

IN OUT

HX? VSUP 1

ENABLE A 8 INPUT 2 9

Final PCB Design (Pi Shield)

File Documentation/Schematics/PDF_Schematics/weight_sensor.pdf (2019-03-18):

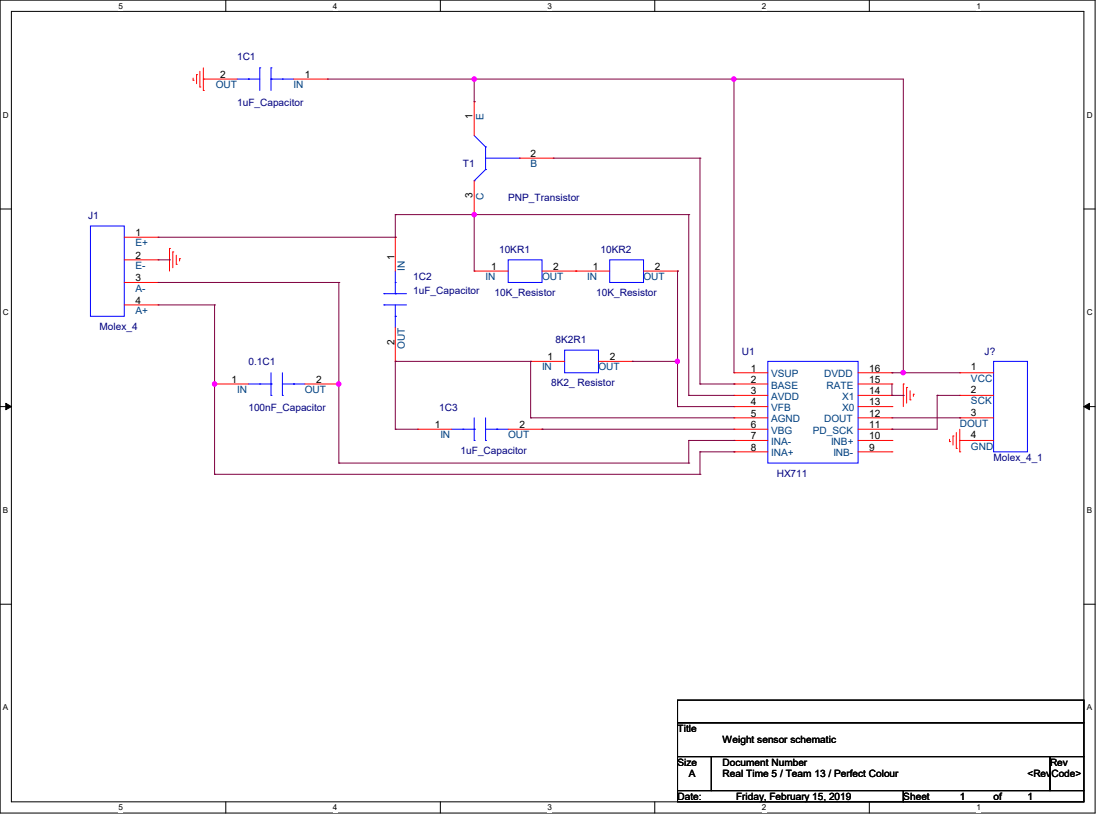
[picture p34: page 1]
A A Title; Size; Document Number; Rev; Date:; Sheet; Real Time 5 / Team 13 / Perfect Colour; <RevCode>; Friday, February 15, 2019; Title; 10K_Resistor; OUT; VSUP 1 BASE 2 AVDD 3 VFB 4 AGND 5 VBG 6 INA- 7 INA+ 8; INB-; INB+; 10 PD_SCK; 11 DOUT; 14 RATE; 15 DVDD; PNP_Transistor; Molex_4; 1uF_Capacitor; 1uF_Capacitor IN; 1 OUT 2; 8K2_ Resistor; Molex_4_1; VCC; SCK; DOUT; GND; 100nF_Capacitor

Weight sensor schematic

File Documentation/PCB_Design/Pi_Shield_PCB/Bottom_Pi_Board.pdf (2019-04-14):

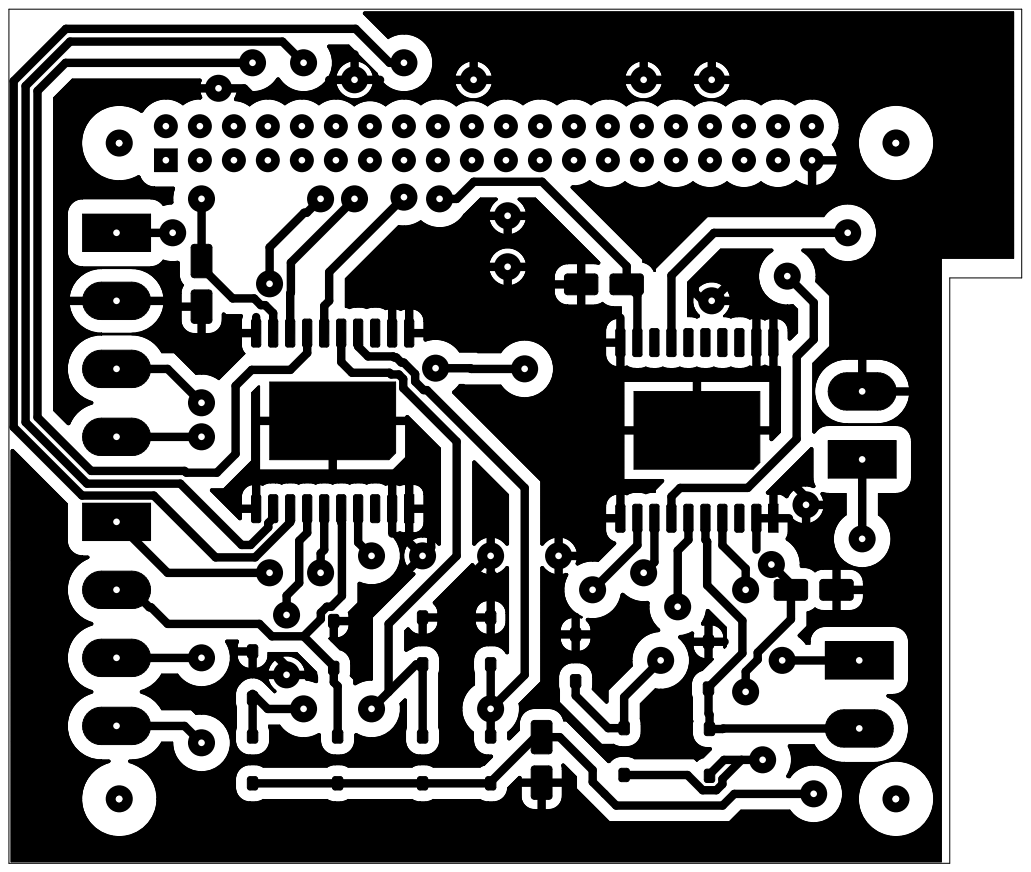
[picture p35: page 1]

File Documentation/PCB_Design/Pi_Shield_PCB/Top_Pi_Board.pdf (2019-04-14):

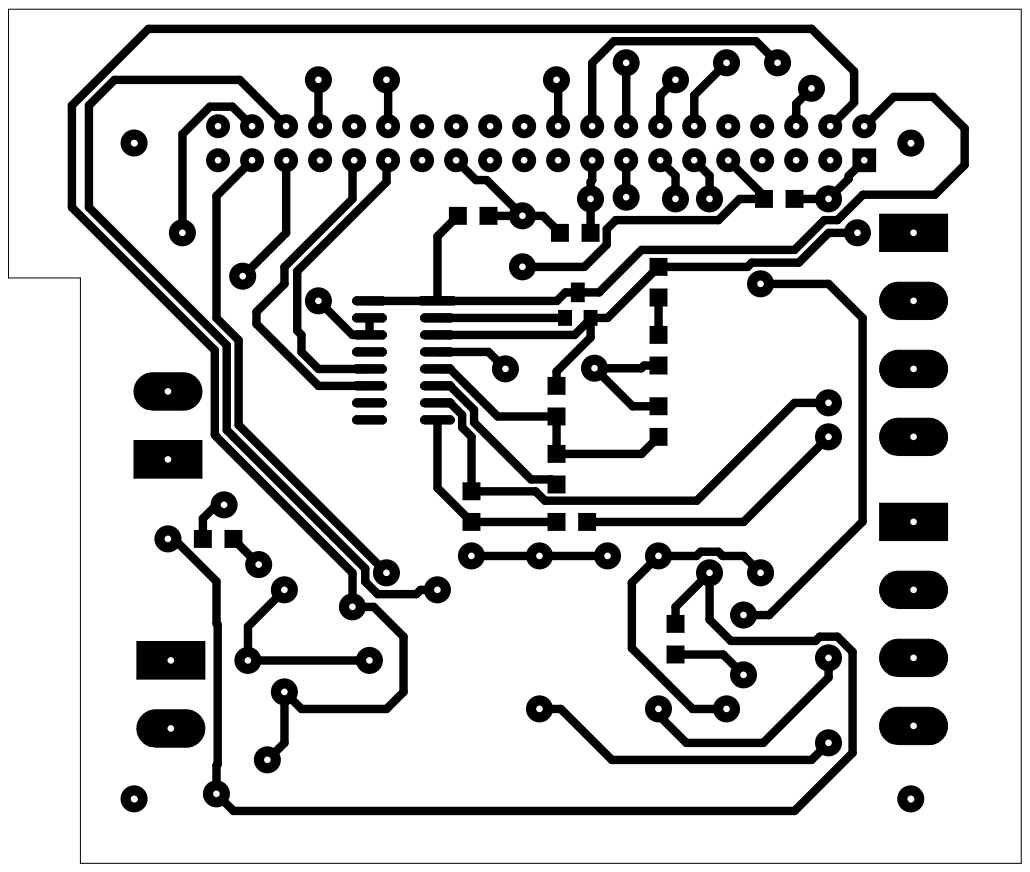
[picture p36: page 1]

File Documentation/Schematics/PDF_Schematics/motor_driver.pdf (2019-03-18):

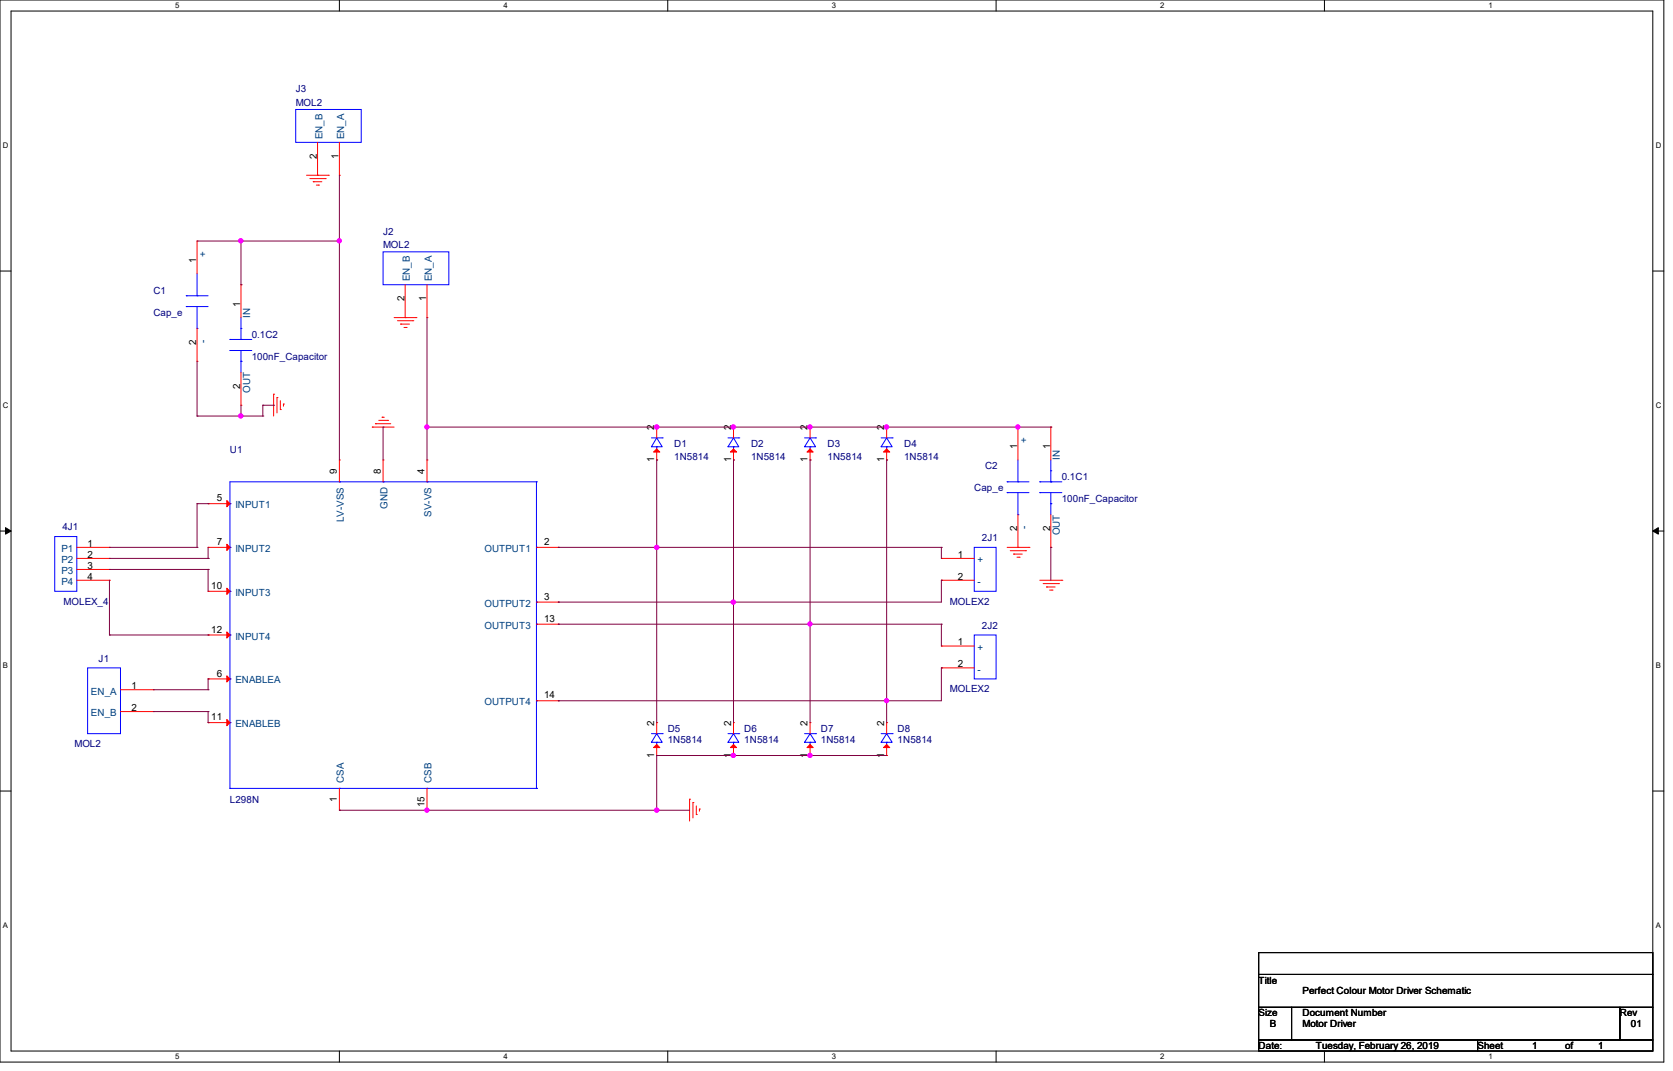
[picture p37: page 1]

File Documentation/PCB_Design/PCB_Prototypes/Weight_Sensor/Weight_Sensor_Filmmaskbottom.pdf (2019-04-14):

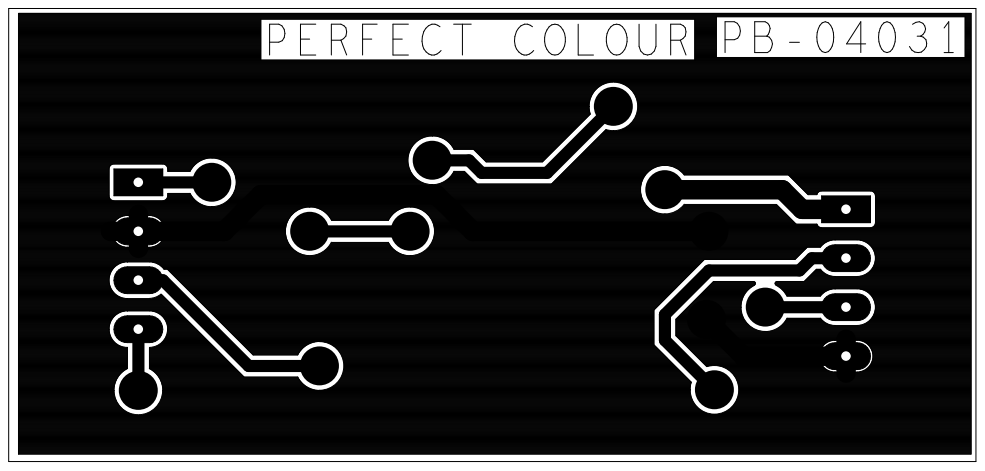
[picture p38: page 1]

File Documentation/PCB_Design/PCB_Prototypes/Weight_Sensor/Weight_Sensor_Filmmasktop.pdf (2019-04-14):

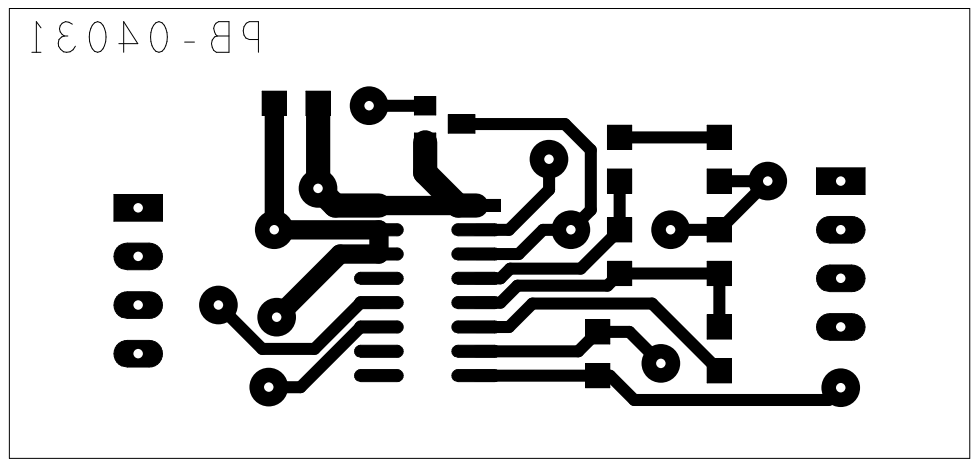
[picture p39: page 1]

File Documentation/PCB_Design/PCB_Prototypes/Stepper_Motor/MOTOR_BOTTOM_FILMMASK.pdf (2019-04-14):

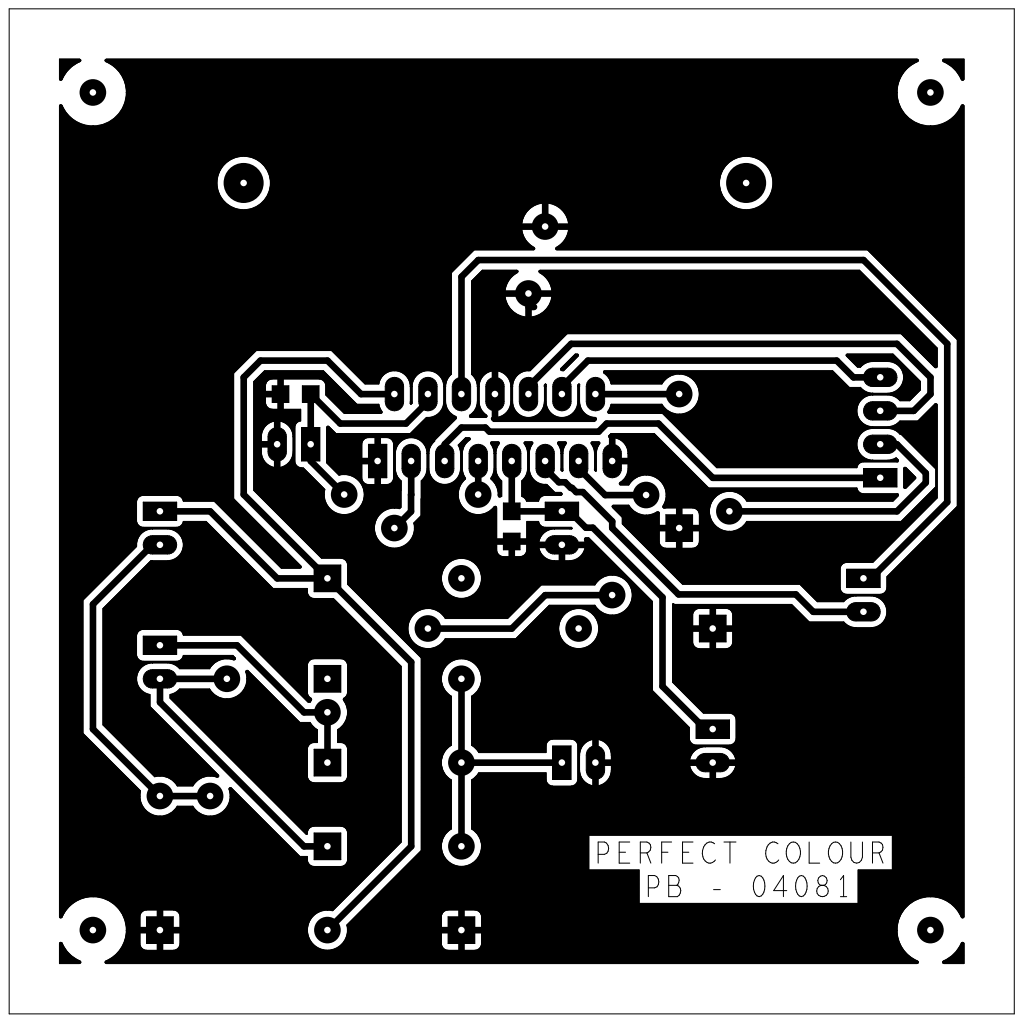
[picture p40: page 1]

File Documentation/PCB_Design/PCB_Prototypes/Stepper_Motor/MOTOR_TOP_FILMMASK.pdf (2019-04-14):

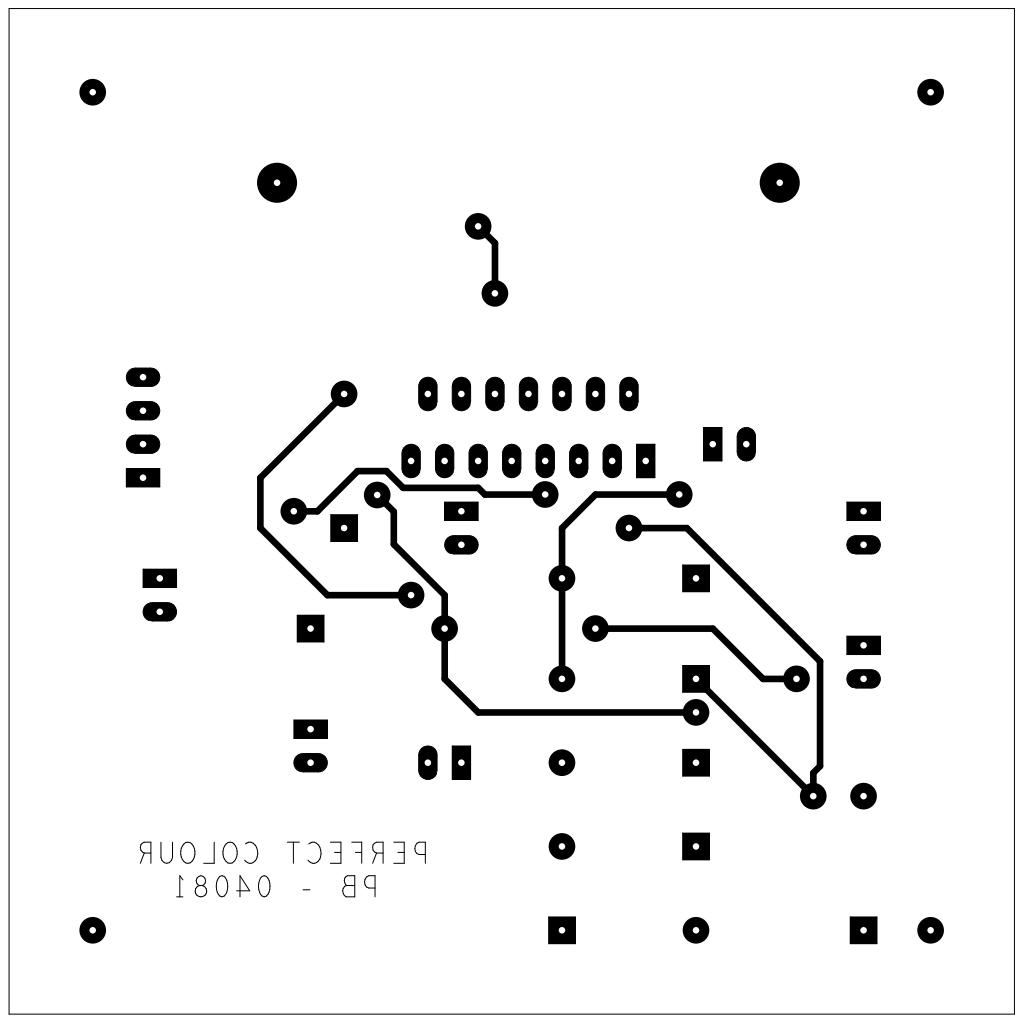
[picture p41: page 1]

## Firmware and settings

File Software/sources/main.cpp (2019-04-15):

/*! \mainpage This is the perfect colour software documentation. Contained here are all of the methods and classes used in the project.
 *  
 
 */

#include "includes/mainwindow.h"
#include <QApplication>

int main(int argc, char *argv[])
{
    QApplication a(argc, argv);
    MainWindow w;
    w.showFullScreen();

    return a.exec();
}

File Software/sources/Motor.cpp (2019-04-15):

/**
 * @file Motor.cpp
 * @author Callum Mason + Silviya Ivanova + Leire Froufe Vigara
 * @brief The class Motor provides the functionality to rotate the paints to the appropriate position
 * @date 2019-04-12
 *
 * @copyright Copyright (c) 2019
 *
 */
#include "includes/Motor.h"
#include <wiringPi.h>

//Constructor
Motor::Motor(){}

/*
	Function to initiliase the pins on the pi that connect to the inputs and enables of the L298. Also sets the speed for rotation
*/

void Motor::init(int input1, int input2, int input3, int input4, int firstenable, int secondenable, int speed) {
    
	pin1 = input1;
	pin2 = input2;
	pin3 = input3;
	pin4 = input4;
	time = speed;
	pinMode(pin1, OUTPUT);
	pinMode(pin2, OUTPUT);
	pinMode(pin3, OUTPUT);
	pinMode(pin4, OUTPUT);
	pinMode(firstenable, OUTPUT);
	pinMode(secondenable, OUTPUT);
	digitalWrite(firstenable, HIGH);
    digitalWrite(secondenable, HIGH);
}

/*
	Function used to rotate the stand 72 degrees.
*/
void Motor::rotate() {
	for (int i =0;i<10;i++) {
	step1();
    delay(time);
	step2();
    delay(time);
	step3();
    delay(time);
    step4();
    delay(time); }
}
/*
	Function used to rotate the stand 1.8 degrees.
*/
void Motor::step1() {
	digitalWrite(pin1, HIGH);
	digitalWrite(pin2, LOW);
	digitalWrite(pin3, LOW);
    digitalWrite(pin4, LOW); 
}
/*
	Function used to rotate the stand 18 degrees.
*/
void Motor::step2() {
     digitalWrite(pin1, LOW);
	digitalWrite(pin2, LOW);
	digitalWrite(pin3, HIGH);
    digitalWrite(pin4, LOW); 
}
/*
	Function used to rotate the stand 18 degrees.
*/
void Motor::step3() { 
    digitalWrite(pin1, LOW);
	digitalWrite(pin2, HIGH);
	digitalWrite(pin3, LOW);
    digitalWrite(pin4, LOW); 
}
/*
	Function used to rotate the stand 18 degrees.
*/
void Motor::step4() { 
    digitalWrite(pin1, LOW);
	digitalWrite(pin2, LOW);
	digitalWrite(pin3, LOW);
    digitalWrite(pin4, HIGH); 
}

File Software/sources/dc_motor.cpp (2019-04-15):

/**
 * @file dc_motor.cpp
 * @author Callum Mason + Silviya Ivanova + Leire Froufe Vigara
 * @brief The class Motor provides the functionality to rotate the paints to the appropriate position
 * @date 2019-04-12
 *
 * @copyright Copyright (c) 2019
 *
 */

#include "includes/dc_motor.h"
#include <wiringPi.h>

  //Constructor
DCMotor::DCMotor() {}

/*
  Function to initiliase the pins on the pi that connect to the inputs and enables of the L298. 
*/

void DCMotor::init() {

  pinMode(24, OUTPUT); // Input 1 Pin 35
  pinMode(27, OUTPUT); // Input 2 Pin 36
  pinMode(25, OUTPUT); // Enable A Pin 37
  pinMode(28, OUTPUT); // Enable B Pin 38
}

/*
  Function used to drive the DC motor forward.
*/

void DCMotor::forward(){
  digitalWrite(24, HIGH);
  digitalWrite(27, LOW);
  digitalWrite(25, HIGH);
  digitalWrite(28, LOW);
}
/*
  Function used to drive the DC motor backward.
*/
void DCMotor::backward() {
  digitalWrite(24, LOW);
  digitalWrite(27, HIGH);
  digitalWrite(25, HIGH);
  digitalWrite(28, LOW);
}


/*
  Function used to stop the DC motor.
*/
void DCMotor::stop() {
  digitalWrite(24, LOW);
  digitalWrite(27, LOW);
  digitalWrite(25, LOW);
  digitalWrite(28, LOW);
}

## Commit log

2019-03-17 Initial test code for testing motor
2019-03-18 Add files via upload
    Schematic for motor driver used to create PCB
2019-03-18 Add files via upload
    Weight sensor schematic used for creating the PCB
2019-03-20 Image of a version of the mechanical model
    Added an image of a version of the mechanical model designed on Solidworks. A few changes have been made since the image and it is currently under construction.
2019-03-25 Weight sensor prints out data
2019-03-25 Fix to printout
2019-03-29 Testing weight sensor
2019-04-01 New library for weight sensor
2019-04-01 Working Weight sensor code and CMake file
2019-04-02 Changed Motor code to be classes
2019-04-02 Parts of the Assembly on CAD
    3D drawings of all the parts of the Perfect Colour Machine. No assemblies are included.
    [1mm tube.SLDPRT, Carouseel axis Rod.SLDPRT, Linear Actuator attachement.SLDPRT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]
2019-04-02 Created Assembly folder
    Will contain the assemblies of the mechanical design.
2019-04-02 Create Assembly
2019-04-04 Added motor rotating functionality to the GUI
2019-04-09 Initial dc motor code
2019-04-11 Changed to work with pi. Only DC motor needs to be added
2019-04-13 Add files via upload
    Final design of PCB which fits on top of the Raspberry Pi as a shield
2019-04-13 DC motor code changed
2019-04-13 Create Weight_Sensor_Prototype
    This folder contains the electronic prototype files used for the weight sensor (schematic and PCB).
2019-04-13 Create Schematics
2019-04-13 Create Stepper_Motor_Prototype
2019-04-14 folder for PCB photos
2019-04-14 Photos of prototype PCB
    For stepper/DC motor and weight sensor
2019-04-14 folder for PCB files
2019-04-14 PCB photos folder
2019-04-14 Photos of prototype PCBs
2019-04-14 folder for PCB prototype design
2019-04-14 Stepper motor PCB prototype
2019-04-14 Weight Sensor PCB prototype
2019-04-14 Stepper motor prototype PCB
    [Stepper_Motor_Prototype.brd]
2019-04-14 weight sensor prototype files
    [Weight_Sensor_Prototype.brd]
2019-04-14 weight sensor prototype PCB
    [Weight_Sensor_Prototype_Board.brd]
2019-04-14 final pi pcb
    [Raspberry_Pi_Shield.brd]
2019-04-15 same name as other file
    [Raspberry_Pi_Shield.brd]
2019-04-15 Pi Shield PCB
    [Shield_for_Pi.brd]
2019-04-15 final design schematic files
    [RASPBERRY_PI_SHIELD.DSN]
2019-04-15 add diodes...
2019-04-15 prototypes folder details
2019-04-15 folder for pdf's of schematics
2019-04-15 schematics pdf's
2019-04-15 Fully working Code with threading
2019-04-15 images - stepper and DC motors and lad cell
2019-04-15 Stepper/DC motor and load cell
